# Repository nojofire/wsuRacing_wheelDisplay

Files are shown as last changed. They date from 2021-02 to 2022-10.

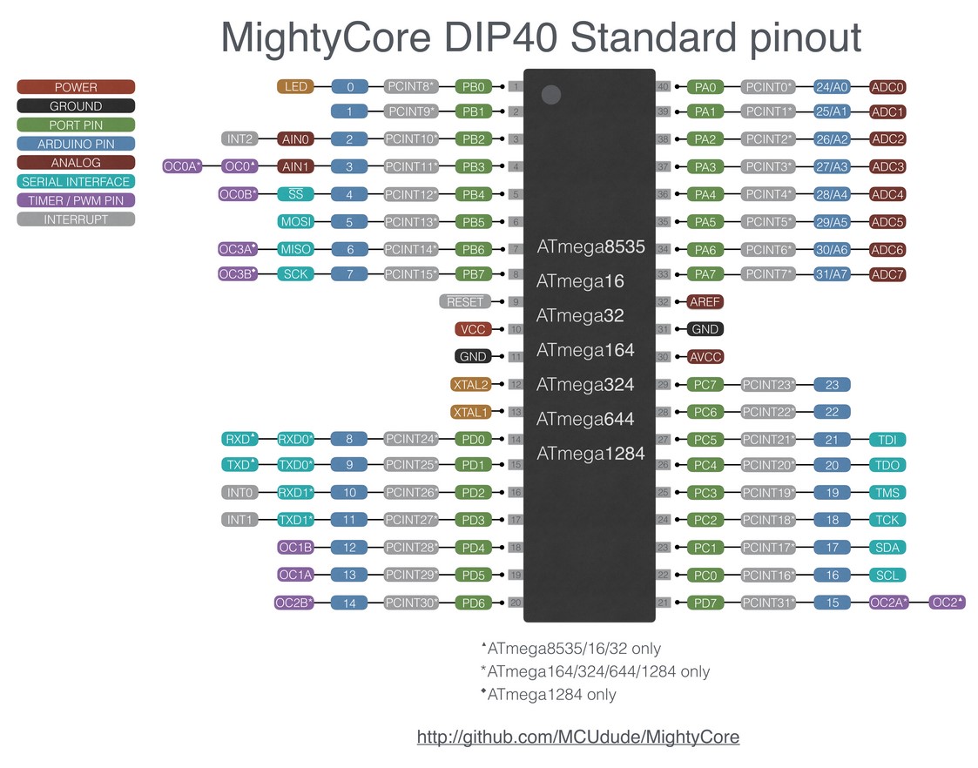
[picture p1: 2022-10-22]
644A pinout.jpg

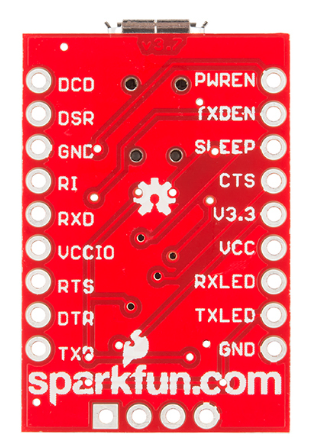
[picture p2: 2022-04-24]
Datasheets/BOB/Backside.png

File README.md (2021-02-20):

# wsuRacing_wheelDisplay
 Files related to my project for Wazzu Racing - 2020-2021

Revision history (starting with V2->V3):

2->3: 	
	
	- After speaking with Clint I found a microcontroller with 2 UART ports to get rid of the
		conflicting I/O lines of the CAN BUS and the USB in. 
		
	- Also Changed from the CH340C to the FT232RL. Reasoning is that the CH340C will not have
    		native USB drivers on machines, documentation is more difficult to find and not as detailed,
		and chip availability is very uncertain. In general the compatability issue woudn't be a big
		deal, but I'm probably not going to be the only person to work on this. The FTDI chip (FT232RL)
		will have native windows support, is a more reliable product in terms of supply and support for
		potential issues, and has better documentation. Only downside is that the cost is much higher:
		the CH340C can be found for around 60 to 80 cents per chip where the FT232RL is around $2.50 a
		pop. We're only making a few of these at most so the cost is negligable.
		
	- Switched out the AZ1117 5V to 3V3 reg. and put in place a 12V to 5V and a 12V to 3V3 linear
		regulator. Both of the LD1086 line of regulators.
		
	- In place of the Crystal we have the ASDMB - 16.0000 MHz - LC Oscillator. Clint said the
		issue with crystals is balancing the capacatance of the wires after a reset (if I interpreted
		what he said correctly). To avoid this we use the oscillator which will give a stable output
		the entire time it's powered (and enabled).
		
	- Adjusted the MAX7219 connections to the LEDs. used to be that DIGIT0 (LSB or right hand
		set of LEDs on the wheel display) had 8 LEDS and DIGIT1 had 7 for a total of 15. I made no
		changes to the quantity but I changed it so that DIGIT1 has 8 and DIGIT0 has 7. This is so the
		code is slightly more readable. So we can just fill a byte from left to right and it will 
		directly coorelate to going from left to right on the LED display. Before we had to adjust
		the code to accomidate the fact that we were first filling up the left 7 bits then then next
		8 bits so we had to have a bit at 0 in the middle of the bytes being shifted out. (we are 
		constrained to a byte of data to send)
	
3->4: (haven't made these changes yet just ideas)
		- Switched the oscillator to one that operates on 5V, and automotive temp range -40C to 125C.
		- Switched to a 5V supply CAN BUS transciever and automotive operating temp range.
		- Got rid of the 12V to 3V3 regulator.
		-

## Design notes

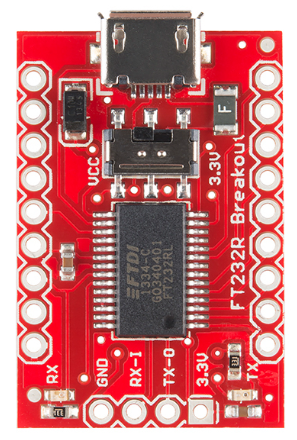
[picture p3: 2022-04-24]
Datasheets/BOB/Frontside.png

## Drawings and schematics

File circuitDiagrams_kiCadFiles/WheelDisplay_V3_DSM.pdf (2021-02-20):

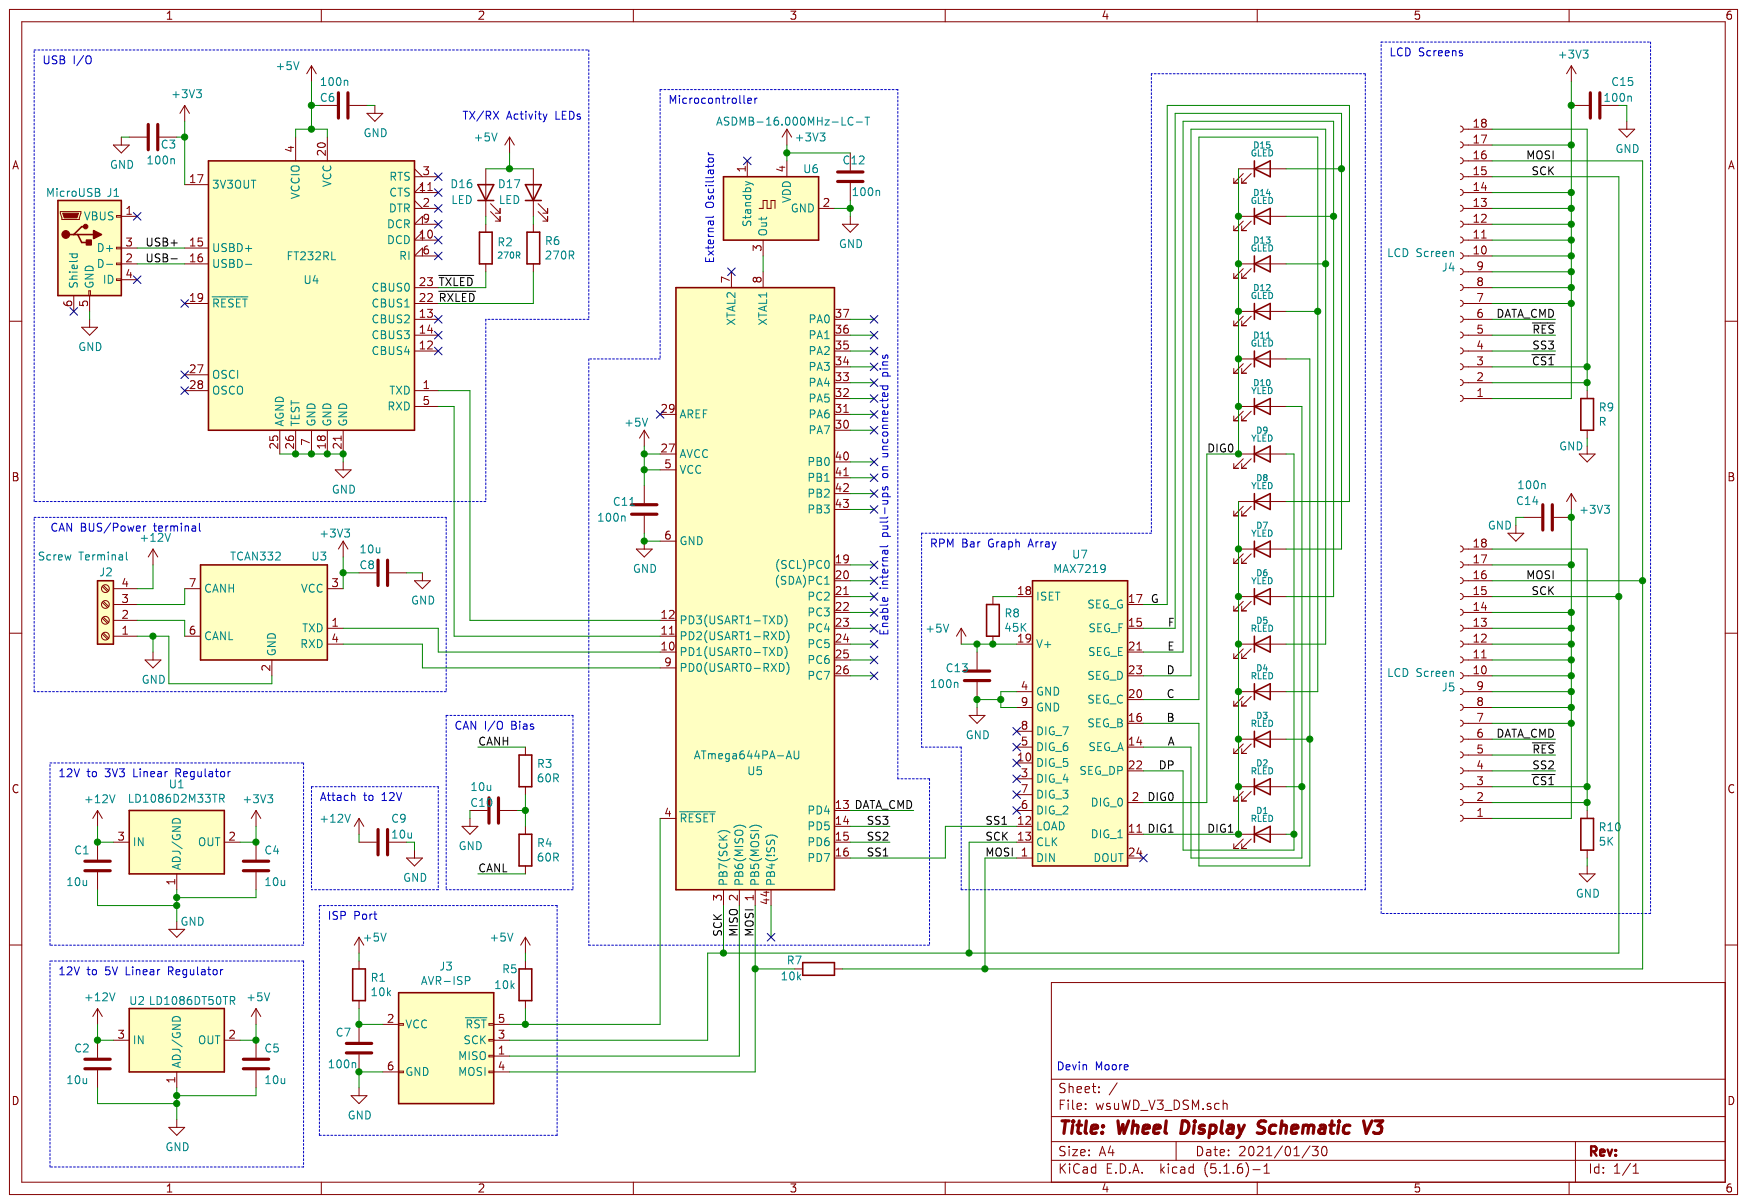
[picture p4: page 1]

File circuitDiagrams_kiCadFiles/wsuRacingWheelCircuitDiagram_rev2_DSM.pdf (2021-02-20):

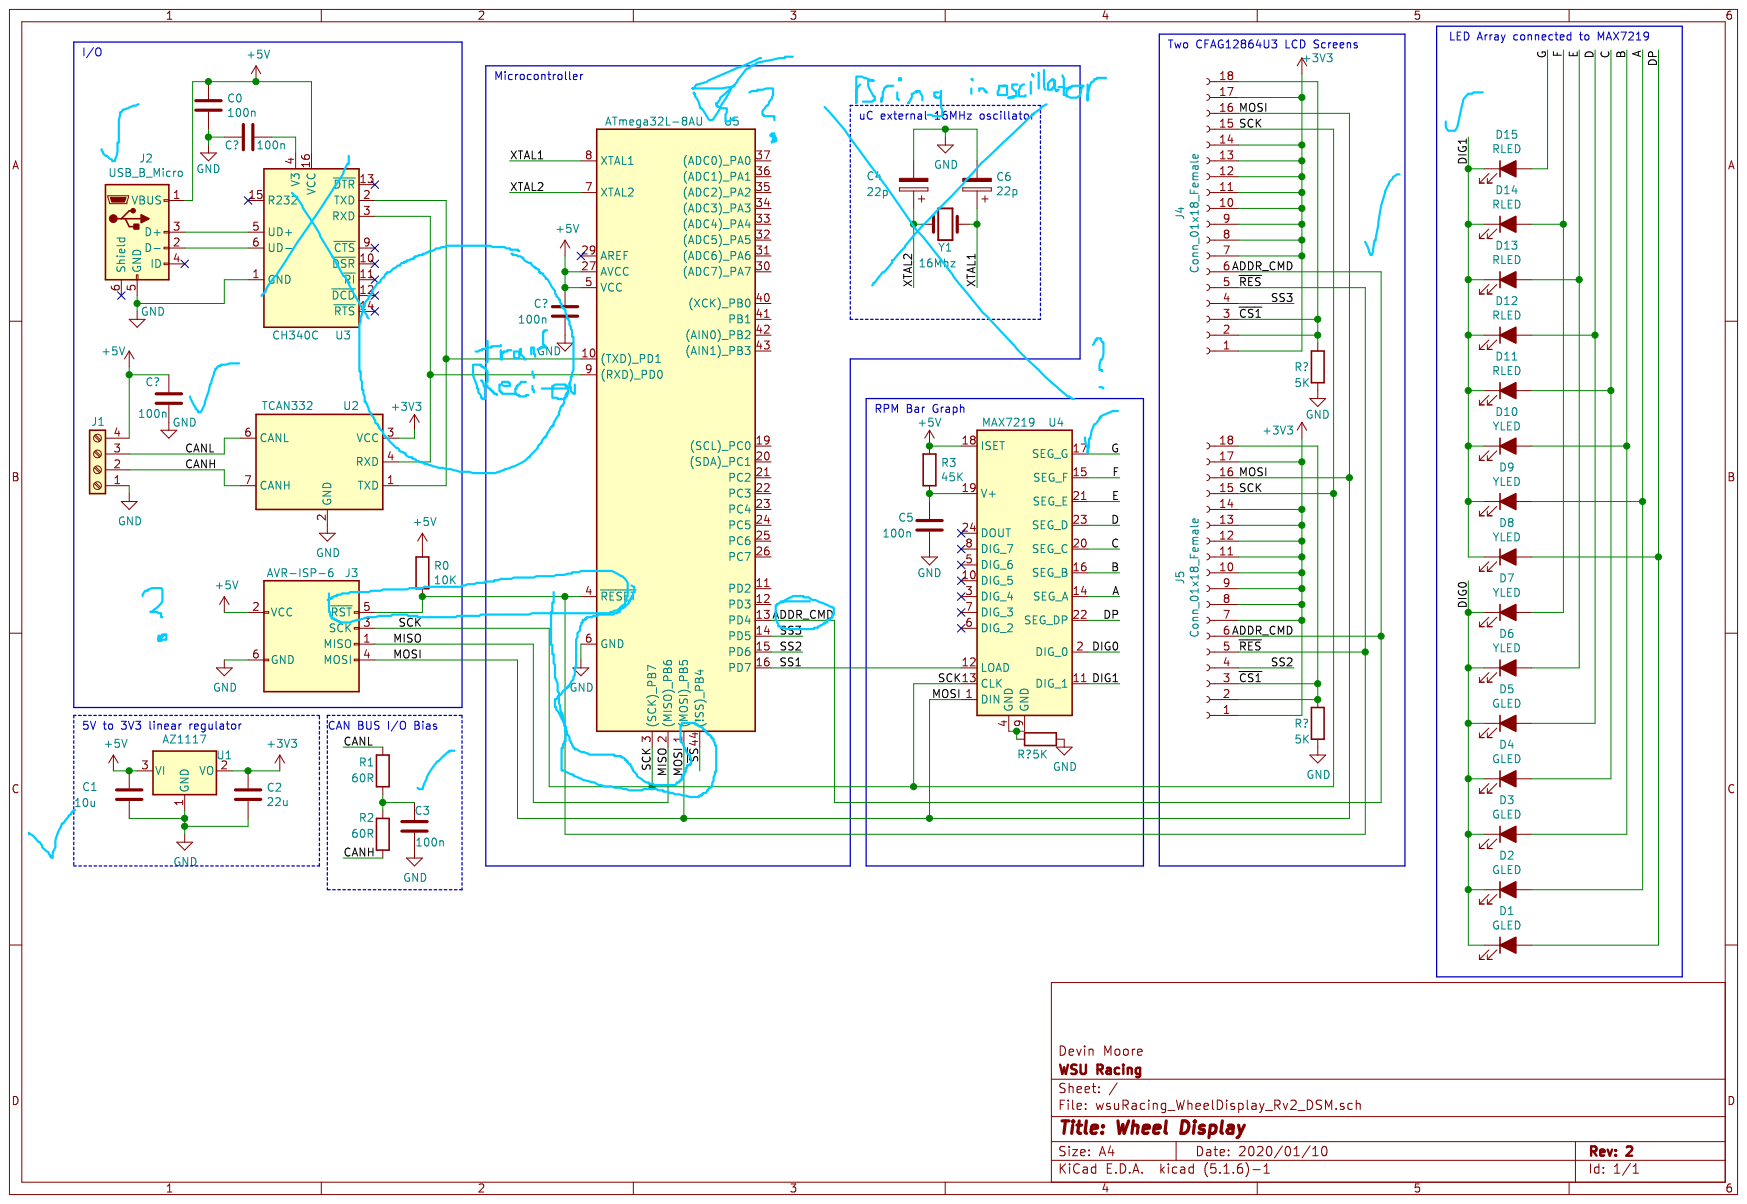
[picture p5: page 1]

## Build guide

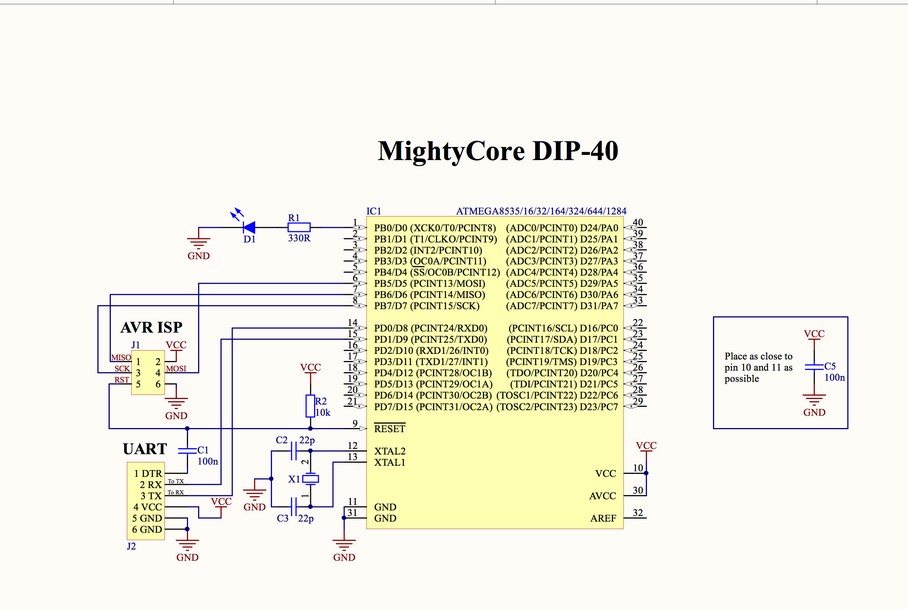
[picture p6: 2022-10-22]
644A wiring help usb programming.jpg

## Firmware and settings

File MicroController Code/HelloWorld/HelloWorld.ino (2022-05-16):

/*
  LiquidCrystal Library - Hello World

 Demonstrates the use a 16x2 LCD display.  The LiquidCrystal
 library works with all LCD displays that are compatible with the
 Hitachi HD44780 driver. There are many of them out there, and you
 can usually tell them by the 16-pin interface.

 This sketch prints "Hello World!" to the LCD
 and shows the time.

  The circuit:
 * LCD RS pin to digital pin 12
 * LCD Enable pin to digital pin 11
 * LCD D4 pin to digital pin 5
 * LCD D5 pin to digital pin 4
 * LCD D6 pin to digital pin 3
 * LCD D7 pin to digital pin 2
 * LCD R/W pin to ground
 * LCD VSS pin to ground
 * LCD VCC pin to 5V
 * 10K resistor:
 * ends to +5V and ground
 * wiper to LCD VO pin (pin 3)

 Library originally added 18 Apr 2008
 by David A. Mellis
 library modified 5 Jul 2009
 by Limor Fried (http://www.ladyada.net)
 example added 9 Jul 2009
 by Tom Igoe
 modified 22 Nov 2010
 by Tom Igoe
 modified 7 Nov 2016
 by Arturo Guadalupi

 This example code is in the public domain.

 http://www.arduino.cc/en/Tutorial/LiquidCrystalHelloWorld

*/

// include the library code:
#include <LiquidCrystal.h>

// initialize the library by associating any needed LCD interface pin
// with the arduino pin number it is connected to
const int rs = 17, en = 18, d4 =20, d5 = 21, d6 = 22, d7 = 23;
LiquidCrystal lcd(rs, en, d4, d5, d6, d7);

void setup() {
  // set up the LCD's number of columns and rows:
  lcd.begin(16, 2);
  // Print a message to the LCD.
  lcd.print("hello, world!");
}

void loop() {
  // set the cursor to column 0, line 1
  // (note: line 1 is the second row, since counting begins with 0):
  lcd.setCursor(0, 1);
  // print the number of seconds since reset:
  lcd.print(millis() / 1000);
}

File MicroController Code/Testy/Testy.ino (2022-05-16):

#include <AsyncTimer.h>
#include <MAX72XX.h>
#include <SPI.h>
#include <MegaCAN.h>
#include <mcp2515.h>

/////CHANGE THESE VALUES TO CHANGE WHAT LIMITER YOU WANT AND THE THRESHOLD//limiter values
int increment = 0;
const int limit = 10000; //absolute limit for displayed value
const int flipper = 400;  //counter value used for flipping modes
int mode = 1;
const double threshold = 0.85; //used to calculate threshold to start blinking

int blinker = 0;
const int blink_limit = 1000; //counter limit to control blinking mode of indicator light
int setting =1;

const extern uint32_t baseID=1512;
const int SS_MAX_DISP = PIN_PD7;
const int MOSI_Pin = PIN_PB5;
const int SCK_Pin = PIN_PB7;

//Segmented Display
MAX72XX SegmentedDisp(SS_MAX_DISP,1);     //defines one max chip
MAX72XXDisplay rpmDisp(&SegmentedDisp,0,8); //defines the chip has 8 digits attatched to it


//CAN set up
const int SS_CAN = PIN_PC0;

//Define frames and Squirt Data
MCP2515 mcp2515(SS_CAN);
MegaCAN megasquirt_can;
MegaCAN_broadcast_message_t mega_Dash;

//Define delay timer
void setup() {
  // put your setup code here, to run once:
  pinMode(PIN_PB0,OUTPUT);
  pinMode(SS_MAX_DISP,OUTPUT); 
  Serial.begin(115200);  
 
  mcp2515.reset();
  mcp2515.setBitrate(CAN_500KBPS,MCP_20MHZ);
  mcp2515.setNormalMode();
  digitalWrite(PIN_PB0,HIGH);
  
}


void loop() {
  can_frame frame;
 
  if(mcp2515.readMessage(&frame) == MCP2515::ERROR_OK){
      megasquirt_can.getBCastData(frame.can_id,frame.data, mega_Dash);
        }
      //if the value is above set values begins blinking mode
      if(mega_Dash.tps >= int(limit*threshold)){ 
        if(increment >= flipper){        
            mode ^=1;
            increment = 0;
          }
          else{
            increment++;
          }
      }
      else if(mega_Dash.rpm <int(limit*threshold)){
        increment = 0;
        mode = 1;
      }
      shiftOn(mega_Dash.rpm,mode);

      //blinking light control
      blinker++;
      
      if(blinker >= blink_limit){
        setting ^= 1;
        blinker =0;
      }
      if(setting == 1){
          digitalWrite(PIN_PB0,HIGH);          
       }
       else if(setting == 0){
          digitalWrite(PIN_PB0,LOW);
       }
  }

void shiftOn(int value, int mode){
    if(mode){ //mode one: Displays numbers to 7seg display
    rpmDisp.writeNumber(mega_Dash.rpm,MAX72XX::Character::ZERO);
    rpmDisp.update();
    }  
    else{ //mode two: Displays all blanks to 7zeg display
      rpmDisp.fill(MAX72XX::Character::BLANK);
      rpmDisp.update();
    }
   }

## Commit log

2021-02-20 Adding files to git
    [wsuWD_V3_DSM.kicad_pcb, wsuWD_V3_DSM.sch]
2021-02-20 Added datasheets and cleaned up schematic
    [wsuWD_V3_DSM.sch]
2022-03-31 Initial Upload
    Removed ISP, Displays
    Simplified Diagram
    Added CAN Controller
    [wsuWD_V3_DSM.kicad_sch]
2022-03-31 Added USB A
    [wsuWD_V3_DSM.kicad_sch]
2022-04-13 Update wsuWD_V3_DSM.kicad_sch
    Changed Components and added all footprints
    [wsuWD_V3_DSM.kicad_sch]
2022-04-15 Added BOB to schematic
    Added BOB to schematic
    Now ready for pcb design
    [wsuWD_V3_DSM.kicad_sch]
2022-04-24 Included new datasheets
    [wsuWD_V3_DSM.kicad_sch]
2022-05-16 Rpm code and pdf
    Added in the current rpm 7zeg display Arduino code.
    Along with including all relevant pdfs for chips on the board
2022-10-22 Added wiring
